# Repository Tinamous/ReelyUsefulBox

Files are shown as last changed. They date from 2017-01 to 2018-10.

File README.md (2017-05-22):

Reely Useful Box - SMD Reel storage and dispenser.
==================================================

SMD reel storage and dispenser based on a Really Useful Storage Box.

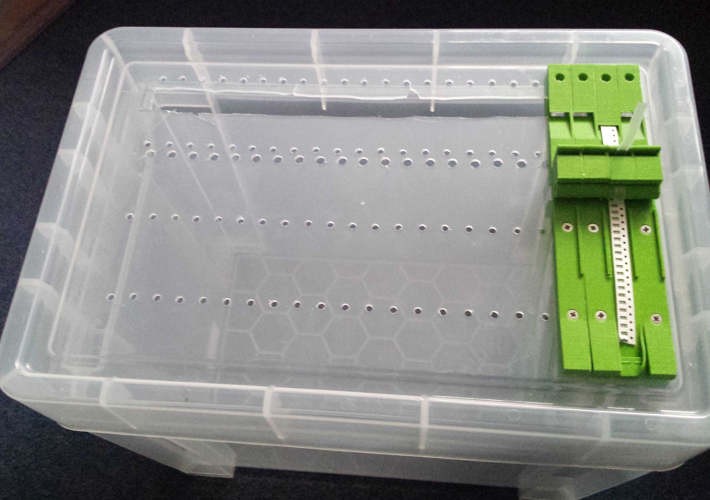
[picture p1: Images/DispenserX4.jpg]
Part built dispenser


Each reel is held and dispensed individually.
The box will hold 25 individual reels (assuming standard 8mm tape for resistors/capacitors).
Each reel holder is 13mm wide. For wider tape/reels this could be doubled to keep to the same hole grid.
Each reel holder is made of 3 different printed parts (1x Top dispenser, 1x reel holder top, 2x reel arms).
Component counter option with LED and photodiode counting of the tape holes.

You can have as few as you want, or as many (well 25 per box and as many boxes as you need).

All design files are Openscad and .stl for direct printing. I found it best to print with a brim as these are long parts and have a tendency to warp at the ends.

##MountingPlate

This is the drilling guide. You can either print it out and drill, or laser cut some acrylic with it.

* Open the .svg file in Inkscape and print this out. 
* It's bigger than A4/Letter, do not scale it! (The box is bigger than A4 length ways so you will need a couple of these for the full 25 way box).
* Stick the sheet to the box lid, allow a margin of about 4mm around the edges where the lid inner curves up (remember the reel holder top has to fit inside).
* Ensure the holes line up with the Dispenser.
* Drill the holes. 
** 4MM for the M3 screw holes (4x).
** 5mm for the LED insert.
** 9-10mm for the square tape hole. This is likely to crack the lid in the process, maybe drill 4 M3.5 holes at each corner and cut, or cut out the entire length of all the sections with a dremel of something  (Be VERY careful if you use a knife, the lid is very tough!).

##Dispenser

This sits on the top of the lid. 

Print in any color you like, you can color code the dispensers to match your components. I'm using:

* 1206 Resistors: Red
* 0805 Resistors: Green
* 1206 Capacitors: White
* 0805 Capacitors: Grey
* 1206 LEDs (Blue): Blue
* Other: Bronze

Original inspiration taken from http://www.thingiverse.com/thing:1080195 with modifications.

* Print this on it's side without supports but with a brim.
* 4 mounting holes for M3 countersunk machine screws.
* A small hole that aligns with the holes in the tape and accepts a 3mm LED underneath.
* The tape film wraps around the block on the top and exits vertically, so pulling the tape film up advances the tape and removes the film.
* Of you can just leave the film on if you want to cut of a section of tape.
* The top block has a hold in the back. Use a M3 heatfit   insert in here if you want to use the component usage sensor block.

## ReelHolder-Top (ReelHolder.scad/ReelHolder.stl)

This sits inside the box to hold the reel arms and is screwed to the lid with the dispenser on the top.

* Print without supports but with a brim as this tends to warp at the edges.
* Fit 3x or 4x M3 HeatFit inserts (Do not fit the one by the square cut out if you wish to use the ComponentUsageSensor block.
* The M5 hole allows a 3mm LED to be pushed through into the dispenser 

## ReelHolder-Arm

These hold the reel and is mounted in the ReelHolder-Top.

* Print 2x of these for each arm.
* These push together either side of the reel and the ReelHolder-Top
* For the end ones you may wish to use a M3 HeatFit insert and small machine screw to hold the tops together if you don't have a tight fit.
* If the arms are not a good fit together change the value of cyinderMatingTollerance in the OpenScad file. I found 0.4 worked well, 0.2 was very tight.
* You may also like to shorten these arms. The variable armHeight sets the length of these. 150mm should allow the reel to be pulled to one side to be replaced.

## Parts Required:

* M3 Heatfit insert Part 1010655 http://www.insertsdirect.com/cgi-bin/sh000001.cgi?WD=1010655&PN=unheaded-heatfit-insert%2ehtml#a1010655
* M3 x 20mm countersunk machine screw (x5 per reel)
* M3 x 6mm countersunk machine screw (x1 for end reels only, or x2 per reel if you need to keep the reel arms together).
* 19XL Really Useful Box http://www.ryman.co.uk/really-useful-storage-box-19xl-litre
* PLA.
* Drills: 4mm, 5mm, 9 or 10mm.
* SMD devices on reels!

## Printer Settings

* Printer: Ultimaker 2 Extended+
* Print Sequence: One at a Time
* Profile: Fast print
** Layer Height: 0.15
** Infil: 20%
** Speed: 60 mm/s
** Wall Thickness: 0.7mm
** Top/Bottom Thickness: 0.75mm
* Build Plate Adhesion: Brim
* Support: None

## Electronics

The dispenser is designed to have a LED/PhotoTransistor pair either side of the tape to count the holes in the tape as they pass. See PCB folder for
instructions on the counter and LED PCB.

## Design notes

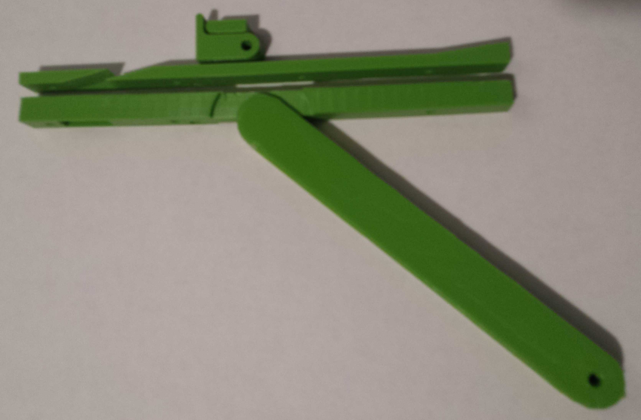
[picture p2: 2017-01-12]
Images/FittingTogether.jpg

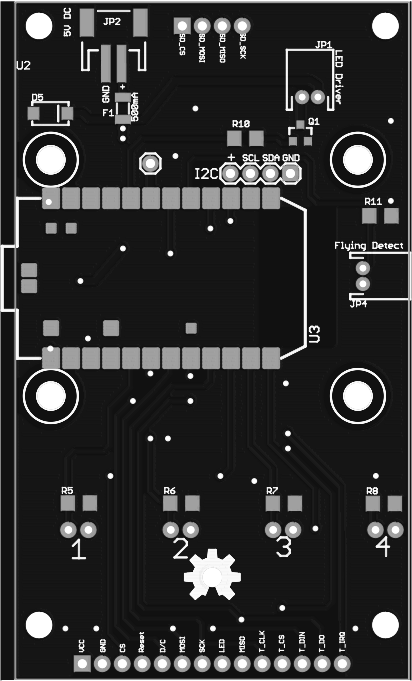
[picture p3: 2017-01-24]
PCB/Images/top.png

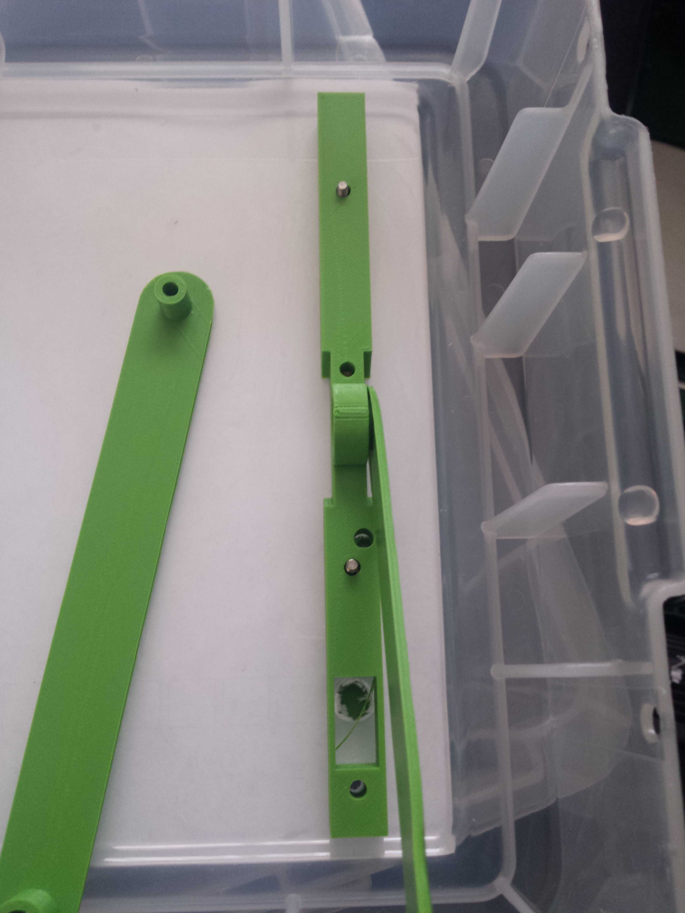
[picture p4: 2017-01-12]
Images/FittingTheArms.jpg

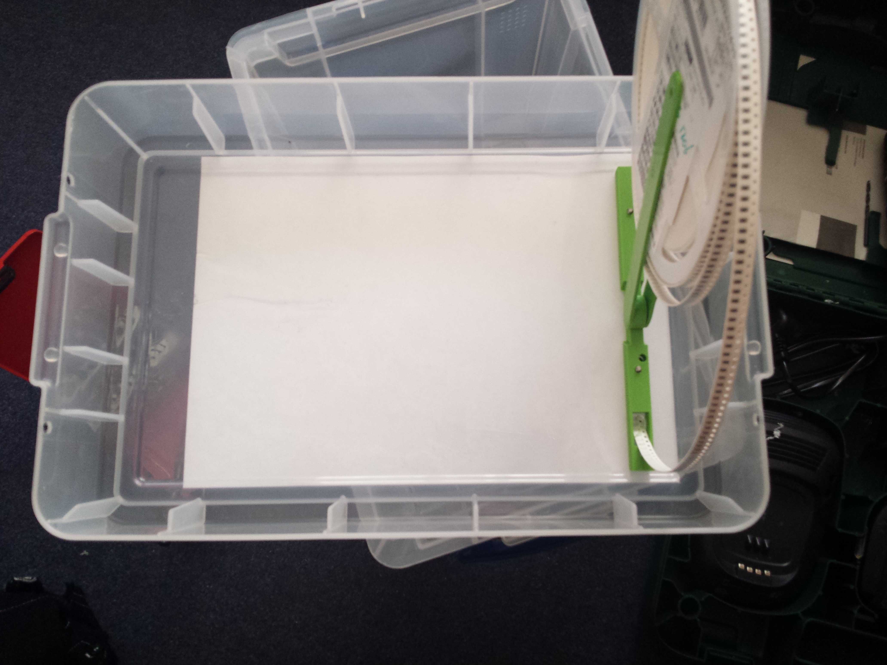
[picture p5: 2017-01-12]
Images/ReelHolderUnderneath.jpg

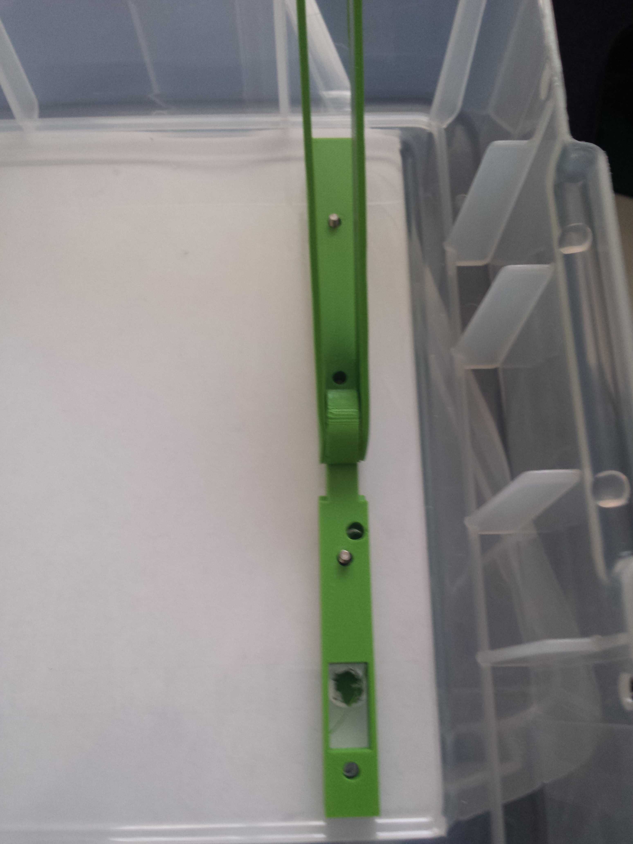
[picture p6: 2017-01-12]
Images/ReelHolderTop.jpg

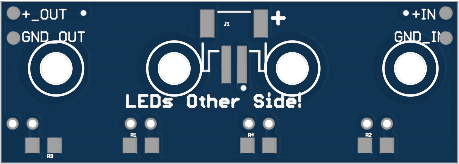
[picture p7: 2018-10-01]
PCB/Images/V2/leds_top.png

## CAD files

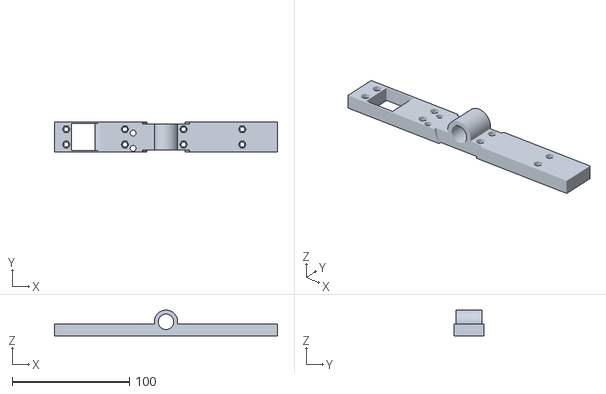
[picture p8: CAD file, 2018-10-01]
13mmVersion/ReelHolder-2Wide.stl
190.0 x 25.9 x 22.0

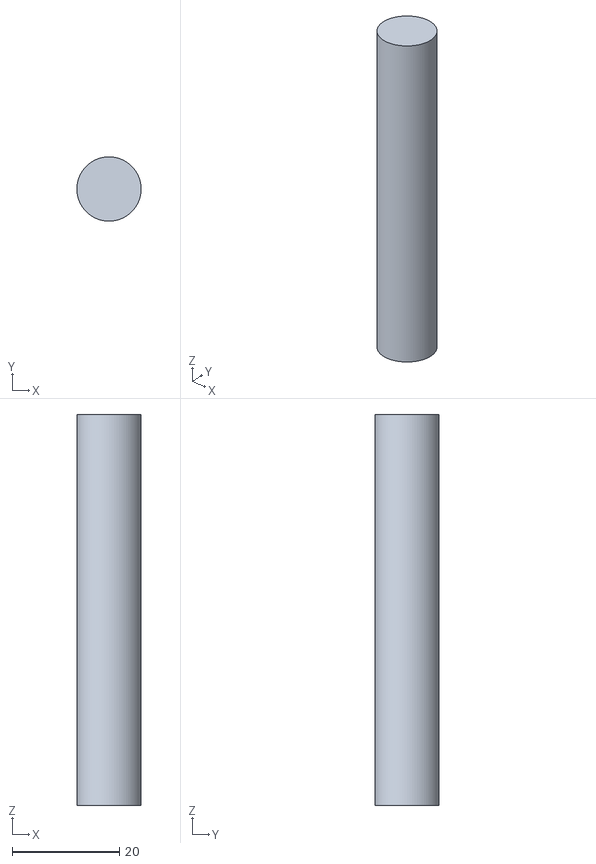
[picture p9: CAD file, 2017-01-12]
Alternative/ReelRod.stl
12.0 x 12.0 x 73.0

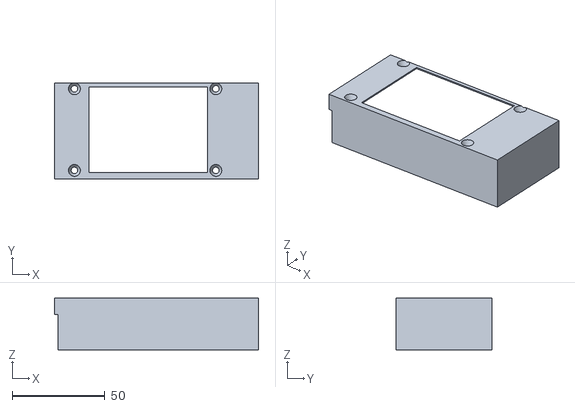
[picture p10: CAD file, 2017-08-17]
Case/DisplayCase.stl
110.0 x 51.5 x 28.0

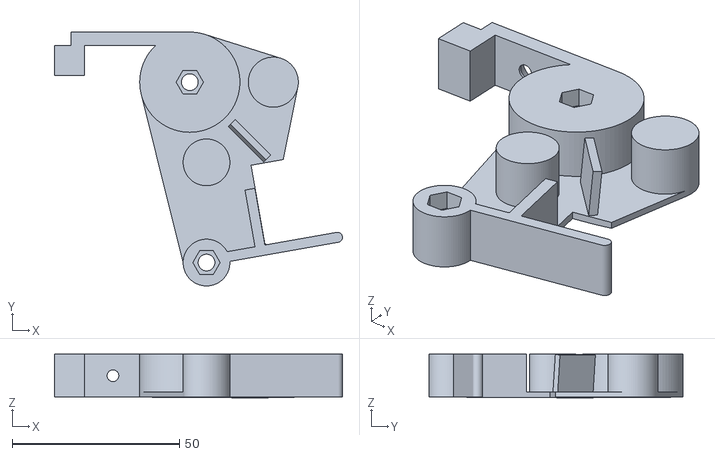
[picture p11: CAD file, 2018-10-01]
ComponentCatcher-13mm.stl
86.2 x 76.0 x 13.0

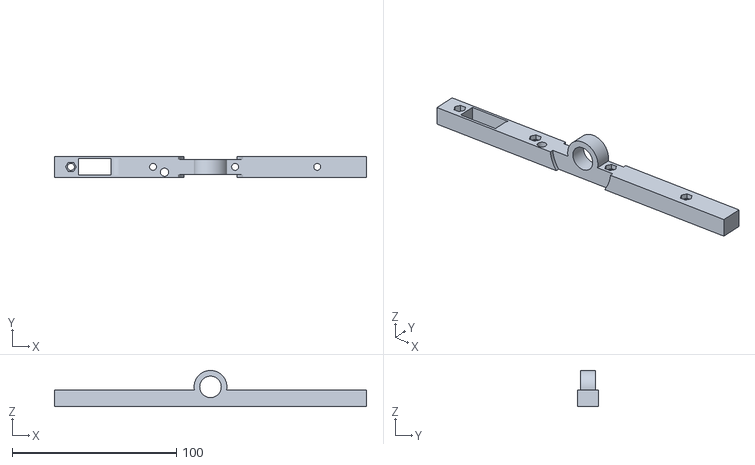
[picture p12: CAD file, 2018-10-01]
13mmVersion/ReelHolder.stl
190.0 x 12.8 x 22.0

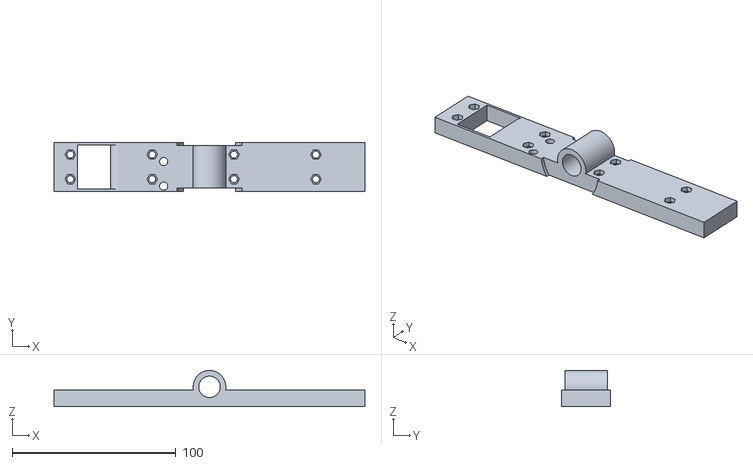
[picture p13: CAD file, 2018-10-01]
ReelHolder-2Wide.stl
190.0 x 29.9 x 22.0

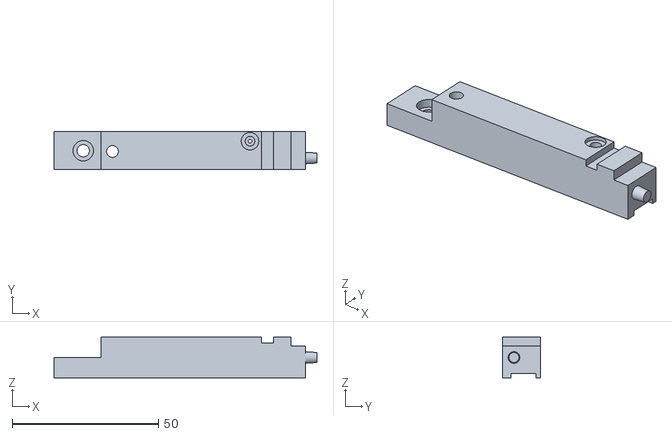
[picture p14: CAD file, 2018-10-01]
13mmVersion/ComponentUsageSensor-Pin.stl
89.9 x 12.8 x 14.0

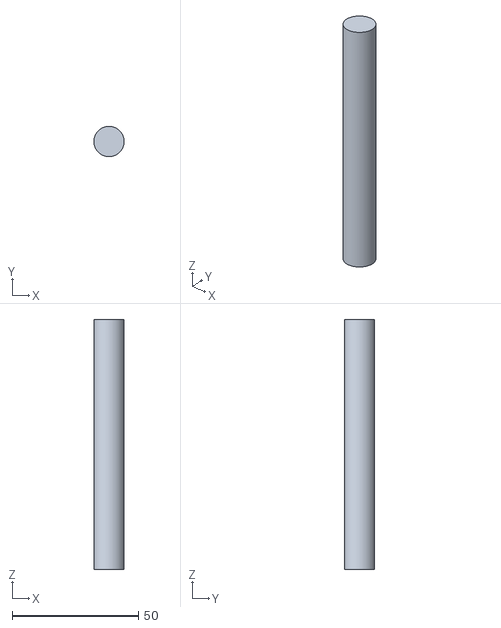
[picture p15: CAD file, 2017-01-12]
Alternative/ReelRod-x7.stl
12.0 x 12.0 x 99.0

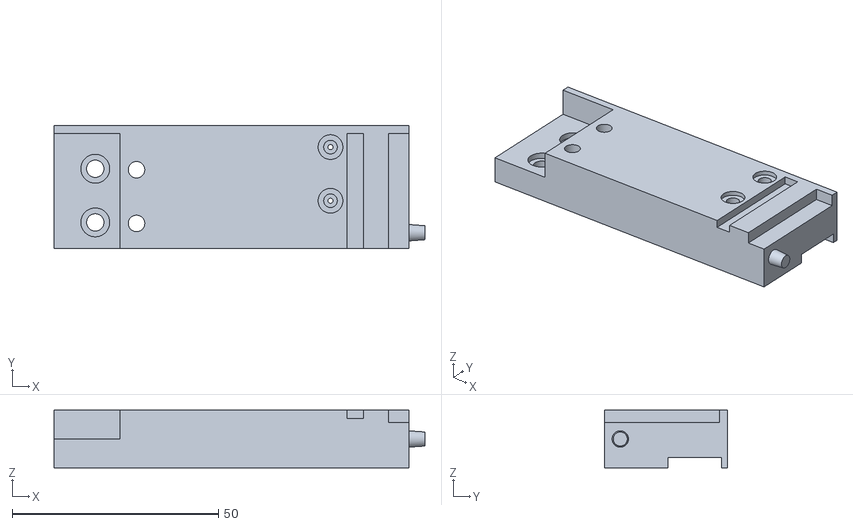
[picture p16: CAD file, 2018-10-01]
ComponentUsageSensor-Pin-LED.stl
89.9 x 29.9 x 14.0

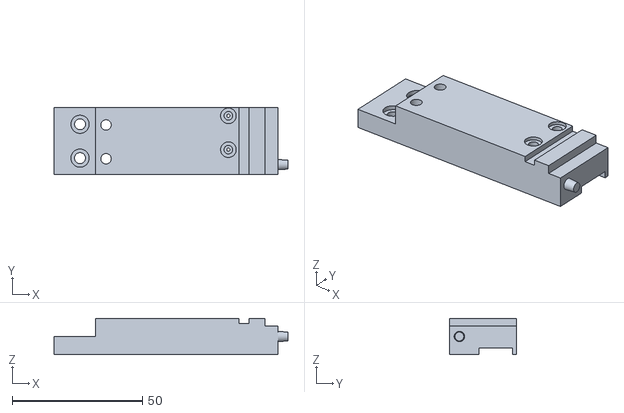
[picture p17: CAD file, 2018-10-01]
13mmVersion/ComponentUsageSensor-Pin-LED.stl
89.9 x 25.9 x 14.0

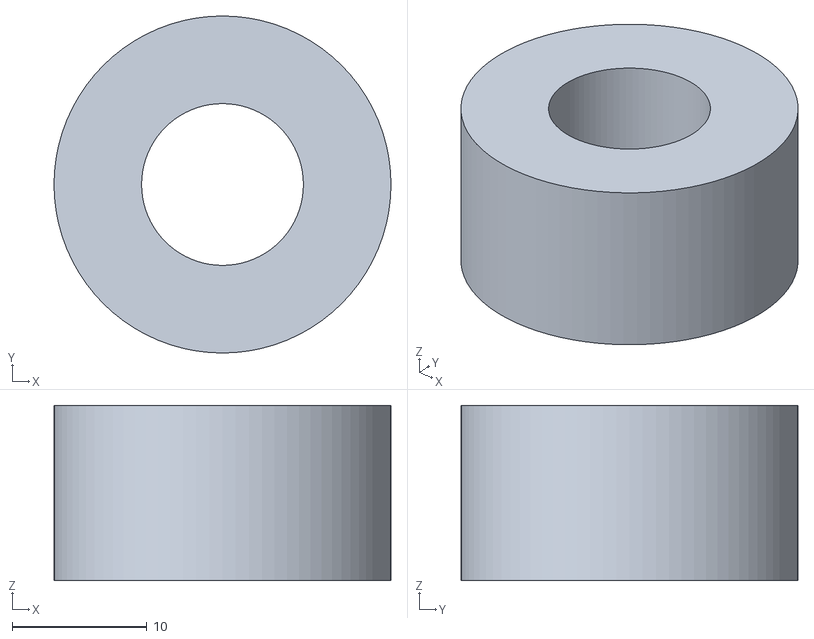
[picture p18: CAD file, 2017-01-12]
Alternative/ReelBlank.stl
25.0 x 25.0 x 13.0

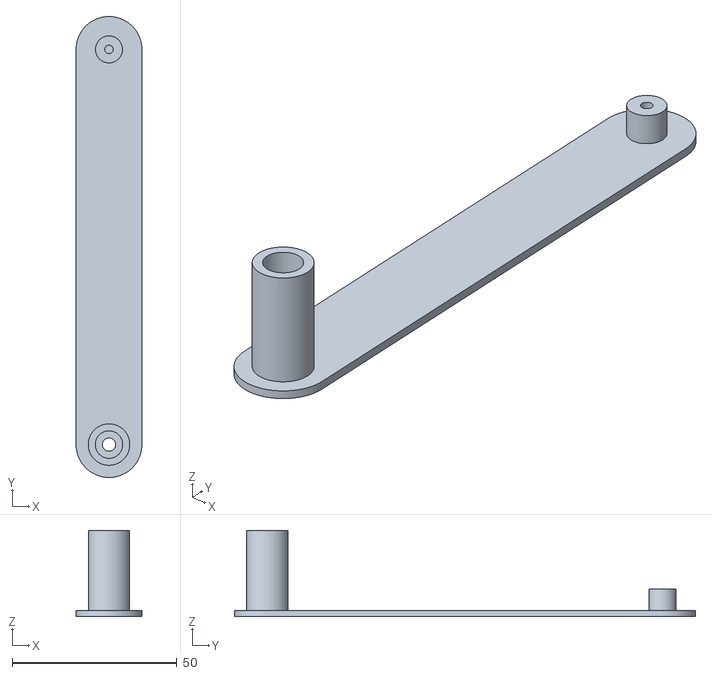
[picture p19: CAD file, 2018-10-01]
ReelHolderArm-2Wide.stl
20.0 x 140.0 x 26.1

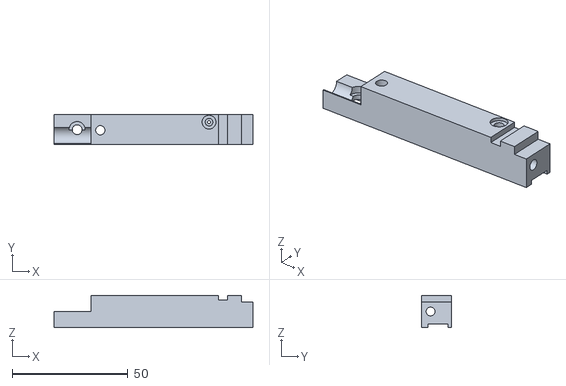
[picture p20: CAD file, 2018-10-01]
13mmVersion/ComponentUsageSensor.stl
86.0 x 12.8 x 14.0

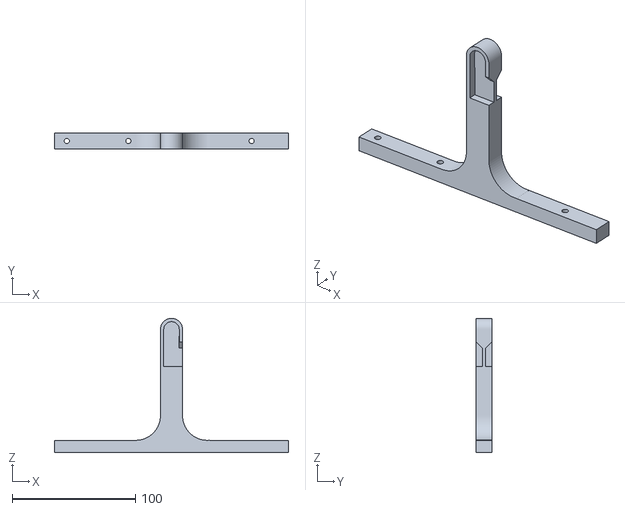
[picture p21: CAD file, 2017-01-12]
Alternative/ReelHolder.stl
190.0 x 13.0 x 109.0

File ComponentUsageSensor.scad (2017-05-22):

$fn = 100;

include <Common.scad>;

// How big or small of a hole to make for the light to come through
// This is printed on its side so allow for printer filament to run in.
tapeHoleSize = 2; // mm - hole side to use for the tape hole light.

// How far before the main block the hole for tape sensing should be.
tapeHoleOffsetFromBlock = 3;

// This should match the roll over block height
// excludes the tape gap.
bodyHeight = 14;
echo("bodyHeight",bodyHeight);

// How long on the x axis this is.
// From Dispenser.
// blockXOffset = 70;
//length = 102; block offset is 87mm
length = blockXOffset - 1; //86; // Or 85?

echo("blockWidth",blockWidth);
actualWidth = blockWidth * numberOfBlocksWide;

// This is 0.5mm less than the main dispenser so that
// the tape doesn't hit as it enters the dispenser.
tapeGap = smdTapeGap +1; // - 0.5;

usePinMount = true;


// Tape Width MUST be set appropriatly
// for numberOfBlocksWide>1 it is assumed this is for
// wide tape and not just to make n blocks in one go.
// Hence tapeWidth must be set for the tap to ensure
// the tape is guided properly.
module cutoutTapePath() {
    // Fattest part is on the right y=0)
    translate([-0.1,blockWidth - (backerWidth + tapeWidth),-0.1]) {
        //#cube([length+1.2, tapeWidth, tapeGap+0.2]);
    }
    
echo ("blockWidth=",blockWidth);
echo ("backerWidth=",backerWidth);
echo ("tapeWidth=",tapeWidth);
echo ("Left offset=",blockWidth - (backerWidth + tapeWidth));
    
    // Put a very slight angle on the block so that the tape comes out
    // at a lower height than would be expected for the smdTapeGap
    // in the dispenser block - so it shouldn't get stuck when feeding through.
    translate([-0.1,actualWidth - (backerWidth + tapeWidth),0]) {
        rotate([0,1,0]) {
            cube([length+0.1, tapeWidth, tapeGap]);
        }
        //translate([0,blockWidth - backerWidth ,0]) {
    }
}

module cutoutMultiTapePath() {
    // Put a very slight angle on the block so that the tape comes out
    // at a lower height than would be expected for the smdTapeGap
    // in the dispenser block - so it shouldn't get stuck when feeding through.
    
    for (rep = [1 : numberOfBlocksWide]) {
        width = blockWidth * rep;
        translate([-0.1,width - (backerWidth + tapeWidth),0]) {
            rotate([0,1,0]) {
                cube([length+0.1, tapeWidth, tapeGap]);
            }
            //translate([0,blockWidth - backerWidth ,0]) {
        }
    }
}
   
// Make a sticky out pointy thing for mounting to the 
// dispenser block.
module mountingPoint() {
    
        // No repetition for multiblocks.
        // Fixed at 7mm up
        translate([length - 0.1, 4, 7]) {
            rotate([0,90,0]) {
                // Component counter mount hole
                // Hole is 4.2mm
                cylinder(d1=4, d2=3.4,  h=4);
            }
    }
}

// Use either this or the mounting point
module horizontalMountingHole() {
// Horizontal hole.
// 20mm screw. 5mm into nut leaves 15mm in the body.
// Don't make shorter as this 
screwHeadDepth = length - 15;
    
    translate([-0.1, 4, 10/2 + smdTapeGap]) {
        rotate([0,90,0]) {
            // Component counter mount hole
            cylinder(d=3.8, h=length+0.2);
            // Screw head sink in.
            cylinder(d=7, h=screwHeadDepth);
        }
    }
}

// Holes for the module to be mounted onto the dispenser.    
module mountingHole() {

    // Needs to be addeed.
    //mountingPoint();
    
    // If used, needs to be subtracted.
    if (!usePinMount) {
        horizontalMountingHole();
    }
    
    // All vertical holes are on a 13mm pitch
    // so 6.5 from edge.
    // Dispenser first hole is 10mm in.
    translate([10, 6.5, 0]) {
       cylinder(d=4.2, h=bodyHeight);
    }

    // Add a cutout for the screw head.
    // Sink it right in otherwise we need a long screw.
    // as it has to go through the 5mm of the dispenser
    // and the 10mm of the rool holder top.
    translate([10, 6.5, tapeGap + 1.5]) {
        //   
       cylinder(d=7, h= bodyHeight);
    }
}

module lightSensorHole() {
    translate([0,0,0]) {
        translate([70 - tapeHoleOffsetFromBlock, blockWidth - backerWidth - tapeHoleOffset,-0.1]) {
            // Small hole all the way up
            // Tape hole is about 1.75 with 4mm spacing
            cylinder(d=1.25, h=bodyHeight - tapeGap + 0.2);
            
            // Bigger hole at top for the sensor to be pushed into
            // Add 0.3mm on to allow for Form2 tight fit.
            // 3mm worked well for UM PLA.
            translate([0,0, tapeGap + 2]) {
                cylinder(d=3 + 0.3, h=bodyHeight - tapeGap);
            }
            
            // And an even bigger hole for the wide part of the sensor.
            // so that the PCB can sit flush onto the block.
            // LED body length is about 5-6 mm.
            // Allow 1mm only for the top part.
            translate([0,0,bodyHeight - 1]) {
                cylinder(d=6, h= 2);
            }
        }
    }
}

// Holes (well hole) for the PCB to use when mounted on-top
// NB: Block needs to be fixed to the dispenser system 
// before the PCB is attached, and the PCB may be 
// shared between different dispensers.
module pcbMountingHoles() {
    
// Just one mounting hole as the LED/diode is already a mounting point.

// How deep in the screw recess should stop 
screwHoleDepth = 6.5;
    
// PCB has LED at 3mm offset
// however it's actually 3.25 (1.5mm backerWidth wall))
// or 3.75 if we use a 2mm backerWidth wall
// So move the mounting hole so that the distance between the LED hole
// and the mouting hole are the same.
pcbLedOffsetFudge = 0.25;
        
    translate([20,6.5 - pcbLedOffsetFudge,0]) {
        //#cylinder(d=8, h= bodyHeight - screwHoleDepth);
        // 6.5 is a little tight for the nut.
        //cylinder(d=6.6, h= bodyHeight - screwHoleDepth, $fn=6);
        
        // Screw head should sit just inside the block above
        // the tape path
        //#cylinder(d=6.6, h= screwHoleDepth);
        // Hole all the way though for the thread.
        #cylinder(d=4, h= bodyHeight + 1.1);
        
        // recess the nut 3.5mm into the part.
        translate([0,0,bodyHeight-7]) {
            #cylinder(d=6.6, h= 2.8, $fn=6);
            
            translate([-5,-5.7/2,0]) {
                #cube([5,5.7,2.8]);
            }
        }
    }
    
    /*
    translate([50,6.5 - pcbLedOffsetFudge,0]) {
        //#cylinder(d=8, h= bodyHeight - screwHoleDepth);
        cylinder(d=6.6, h= bodyHeight - screwHoleDepth, $fn=6);
        cylinder(d=4.5, h=bodyHeight + 0.1);
    }
    */
}

// Remove space for the display pins to protrude through
// blocks.
module pcbPinsCutouts() {
        
    // 3mm in. (This is the top one).
    // It also needs to allow for the LED drive
    // connector which is 12mm down the PCB
    translate([0, 0, bodyHeight-7]) {
        cube([16,blockWidth,7.1]);
    }
    
    // 84mm in. End nearest the dispenser block
    // allow for main display pins.
    translate([81, 0, bodyHeight-3]) {
        cube([6,blockWidth,3.1]);
    }
    
    // Remove space for the OSH LED. 
    // This is only needed on the middle 2 
    // blocks but we don't knowh which two they are.
    oshLedXPosition=73; //mm
    translate([oshLedXPosition-2, 0, bodyHeight-2]) {
        cube([4,blockWidth,2.1]);
    }
}

difference() {
    union() {
        // Main block body.
        cube([length, actualWidth, bodyHeight]);
        
        if (usePinMount) {
            
            if (repeatTape) {
                // repeat pins might cause problems for tollerance.
                for (rep = [0 : numberOfBlocksWide -1]) {    
                    repYOffset = rep * 13;
                    translate([0,repYOffset,0]) {
                        mountingPoint();
                    }
                }
            } else {
                mountingPoint();
            }
        }
    }
    union() {
        if (repeatTape) {
            cutoutMultiTapePath();
        } else {
            cutoutTapePath();
        }
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

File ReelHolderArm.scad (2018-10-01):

$fn=100;


include <Common.scad>;

supportWidth = (blockWidth * numberOfBlocksWide) - 0.25; // To match block width used in the dispenser.

// X Axis length
armLength = 20;
armSupportLength = 2;
armHeight = 120;
armWidth = 1.8; // 0.6mm nozzle

reelTubeDiameter = 12.6;

smallerMatingDiameter = 8;

// How mech space to leave between the inner and outer cylinder.
// 0.2 on UM2+ left a very tight fit.
// 0.3 on UM2+ with RigidInk PLA also a tight fit.
// 0.5 should be easy fit, then use M3 countersunk 12mm screws to join.
cylinderMatingTollerance = 0.5;

// How much to redice the height of the end cylinders to ensure one fits fully in the other
//cylinderHeightTollerence = 2;

module arm() {
    /*
    // Test cube to check assumption on height.
    translate([20,0,0]) {
        cube([10,10,15]);
    }
    */
    
    difference() {
        union() {
            // Fat outer cylinger.
            translate([armLength/2, 0, 0]) {
                translate([0, 0, 0]) {
                    // Create the large outside curved edge.
                    // cut hole in for contersinking M3 screw
                        cylinder(d=armLength, h=armWidth);
                }
                
                // Create a large pin then subtract a small pin
                // + tollerance to allow two ends to mate
                // to hold in place.
                
                translate([0,0,0])  {
                    difference() {
                        union() {
                          cylinder(d=reelTubeDiameter, h=supportWidth - armWidth );
                        }
                    
                        union() {
                            translate([0,0,armWidth]) {
                                cylinder(d=smallerMatingDiameter + cylinderMatingTollerance, h=supportWidth - armWidth);
                            }
                        }
                    }
                }
            }

            
            // Main body
            translate([0,0, supportWidth-armWidth,0]) {
                cube([armLength, armHeight, armWidth]) ;
            }
            
            // Small cylinder end
            translate([armLength/2, armHeight,0]) {
                    translate([0, 0, 0]) {
                       cylinder(d=armLength, h=armWidth);
                    }
                    
                    // Smaller inner mating pin
                    // with hole for M3 brass inser
                    // Keep this short to reduce the maiting surface
                    // area when connected to the fatter cylidner
                    // otherwise it's difficult to seperate
                    smallCylinderHeight = (blockWidth-3);
                    translate([0,0,0]) { 
                        difference() {
                            union() {
                                translate([0,0,0]) { 
                                    // 1mm fudge tollerance.
                                    cylinder(d=smallerMatingDiameter + 0.2, h=smallCylinderHeight - armWidth - 1);
                                }
                            }
                            union() {
                                // Hole to screw into with an M3 machine screw
                                translate([0,0,armWidth]) { 
                                    cylinder(d=3.0, h=smallCylinderHeight + armWidth);
                                }
                                // small countersink to help get the screw started
                                translate([0,0, smallCylinderHeight - armWidth - 1 - 2]) { 
                                    cylinder(d1=3.0,d2=4.2, h=2.01);
                                }
                            }
                        }
                        
                    }
            }
        }
        union() {
            translate([armLength/2, 0, -0.5]) {
                    // Countersink hole at top
                    cylinder(d1=7, d2=3.4, h=armWidth+1);
                    // Ensure the hole runs all the way through
                    cylinder(d=3.4, h=supportWidth+1);
            }
        }
    }
}


//rotate([-90,0,0]) {
    arm();
//}

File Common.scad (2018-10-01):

// Height between base and wrapper.
// for fat components (e.g. LEDs) increase this.
// NB: Tape enterance is not adjusted for this.
smdTapeGap = 2;
// smdTapeGap = 3; // for LEDs

// 1.75mm offset because that's the offset on the tape.
// Was 1.5
tapeHoleOffset = 1.75; // mm

// How thick the back (well side) support structure is
// the tape sits against this.
backerWidth = 1.5; // 1.5;
// 8mm tape + backer = 9.5mm, 
// 13mm block -> 3.5mm play on the left.
// 12mm tape + backer = 13.5 >> block width

// How wide the thing is.
blockWidth = 15;

// How many block units (e.g. 13mm's) wide
// Mounting holes will be duplicated but 
// LED hole not.
// Be sure to set tapeWidth correctly for the wide tape.
numberOfBlocksWide = 1;

// How much to remove off the block width to allow
// for printer tollerance so that each block
// fits in the 13mm grid.
// Set to 6.5 to test screw centers.
// Set to 9.75 to test (3mm offset) for LED for component counter and dispenser.
// Set to 1.5 + 1.75 (3.25) to test (3mm offset) for LED for arm
// Set to 4 to test horizontal coupler.
// Set to 0.25 for normal printing.
blockPrinterTollerance = 0.15; //0.25;

// Tape Width MUST be set appropriatly
// for numberOfBlocksWide>1 it is assumed this is for
// wide tape and not just to make n blocks in one go.
// Hence tapeWidth must be set for the tap to ensure
// the tape is guided properly.

// How much space to allow for the tape.
// Actually 8mm but add 0.5 to allow it to move easily
// LED tape is 12.5mm wide so use 13mm
tapeWidth = 8.5;

// If the tape is to be repeated for each block wide
// typically if making n component sensor blocks in one go 
// e.g. 4 unit block.
// if just wide tape, set to false and set tape width.
repeatTape = true;

// How far along the dispenser the top block
// for film removal is.
// 11mm in the original
// 70mm for the 
//blockXOffset = 70;
// PCB is 86mm long.
blockXOffset = 87;

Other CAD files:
ReelHolderArm.stl
13mmVersion/ComponentCatcher-2Wide.stl
ReelHolder.stl
ComponentCatcher.scad
13mmVersion/ComponentCatcher.stl
13mmVersion/ComponentUsageSensor-Pin-4Wide-MultiTape.stl
13mmVersion/Dispenser-2Wide.stl
13mmVersion/Dispenser.stl
13mmVersion/ReelHolderArm-2Wide.stl
13mmVersion/ReelHolderArm.stl
Alternative/ReelBlank.scad
Alternative/ReelHolder.scad
Alternative/ReelRod.scad
Case/DisplayCase.scad
ComponentCatcher.stl
ComponentUsageSensor-Pin-4Wide-MultiTape.stl
ComponentUsageSensor-Pin.stl
ComponentUsageSensor.stl
Dispenser-2Wide.stl
Dispenser.scad
Dispenser.stl
MountingPlate.scad
MountingPlateV2mm.dxf
MountingPlatev2-smaller-inkscaped.dxf
ReelHolder.scad
ReelHolder2.scad

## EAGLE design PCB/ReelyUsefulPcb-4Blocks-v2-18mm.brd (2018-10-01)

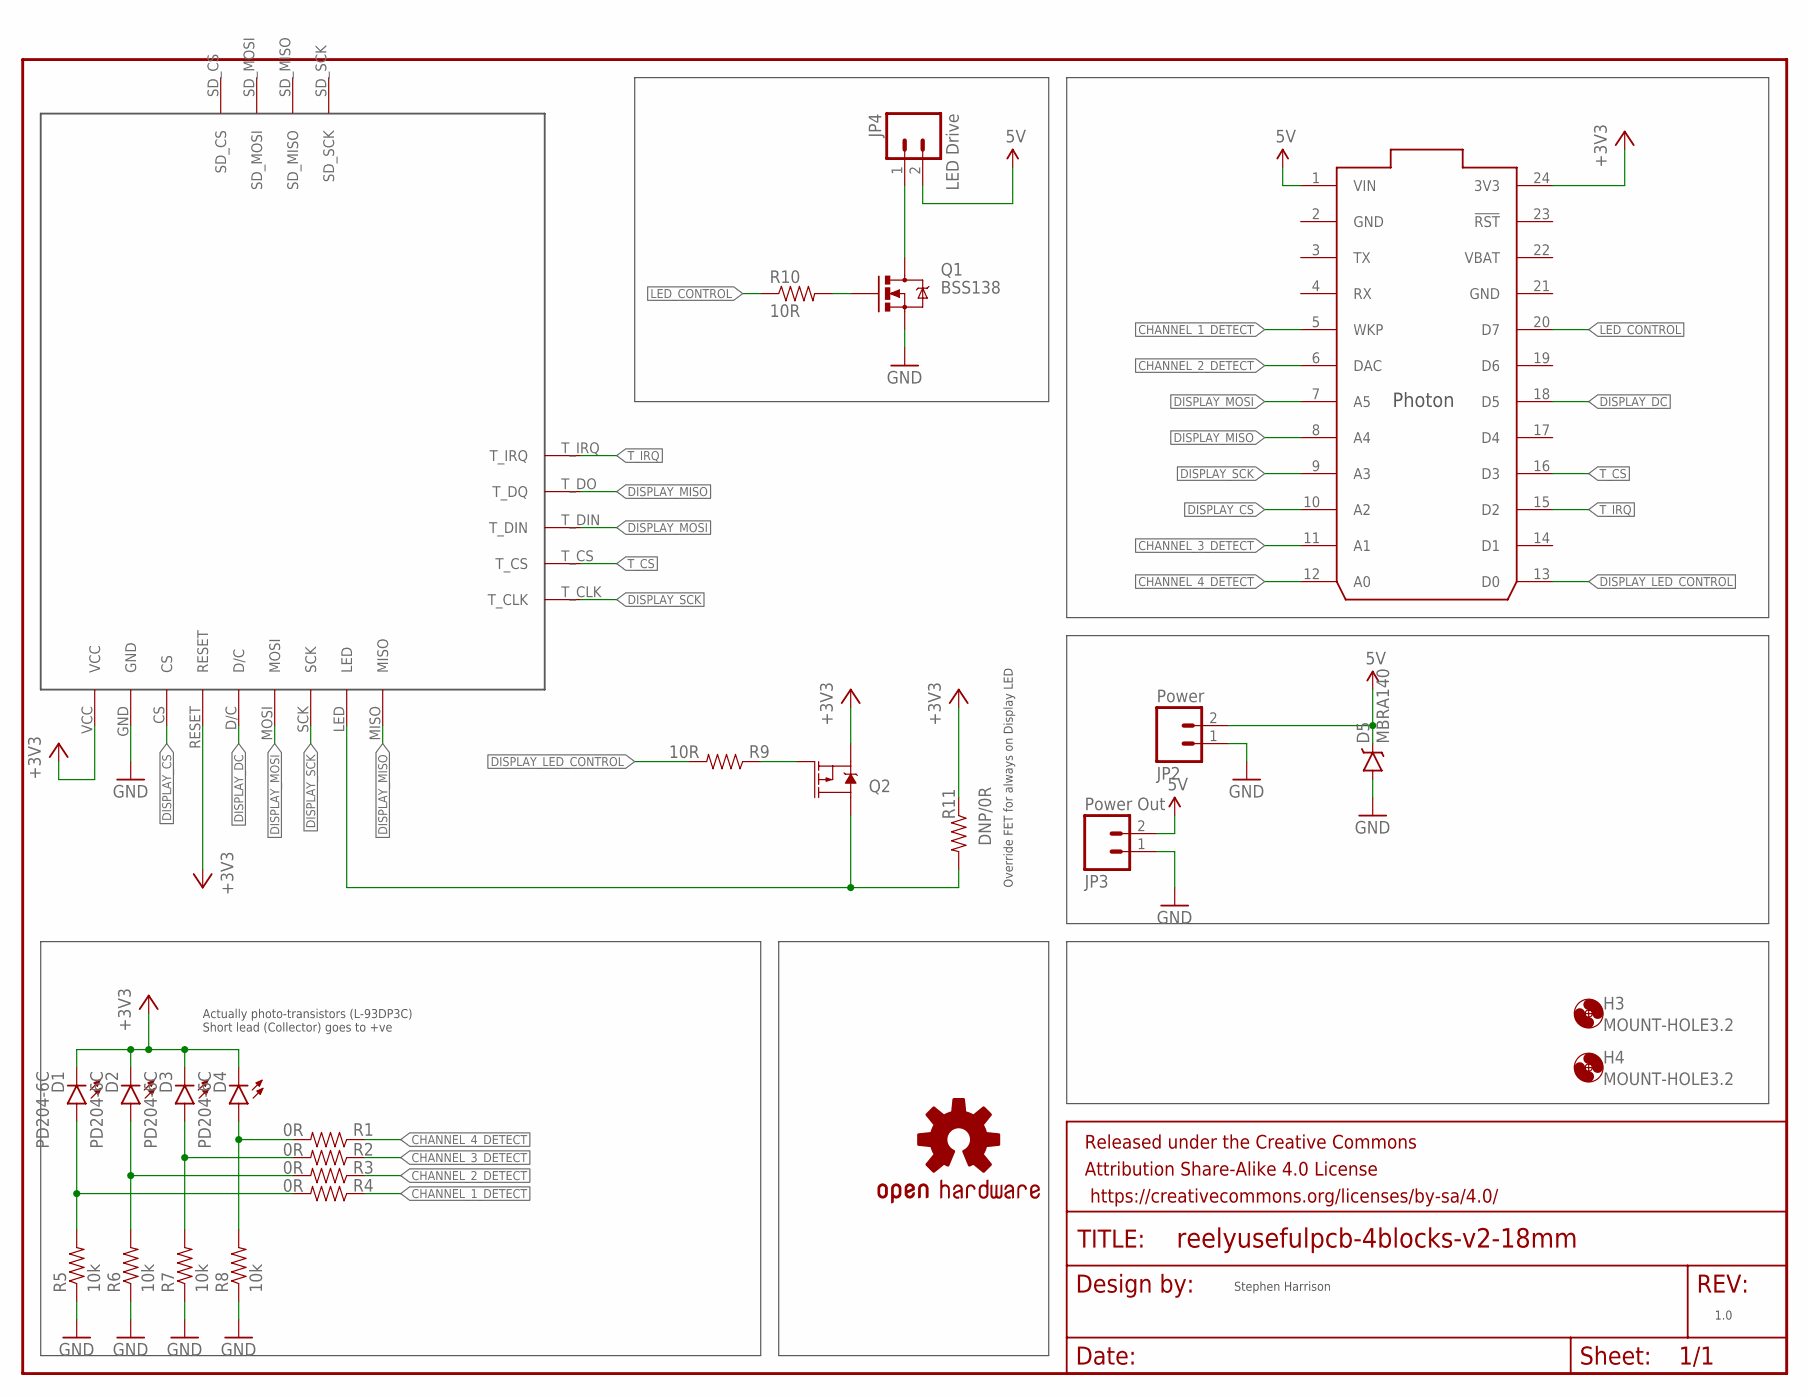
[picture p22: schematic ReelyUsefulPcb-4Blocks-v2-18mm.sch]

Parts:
D1, D2, D3, D4: PD204-6C; LED3MM
D5: MBRA140; SMA-DIODE
FRAME1: FRAME-LETTER; CREATIVE_COMMONS
H3, H4: MOUNT-HOLE3.2; 3,2
JP2: Power; JST-2-SMD
JP3: Power Out; JST-2-SMD
JP4: LED Drive; JST-2-SMD
LOGO1: OSHW-LOGOL; OSHW-LOGO-L
Q1: BSS138; SOT23-3@1; FARNELL 9845330
Q2: 2.5A/30V/105mΩ; SOT23-3
R1, R2, R3, R4: 0R; 1206
R5, R6, R7, R8: 10k; 1206
R9, R10: 10R; 1206
R11: DNP/0R; 1206
U2: TJCTM240NO-MOUNTING-HOMES; TJCTM240-NOHOLES
U3: PHOTON_SMD

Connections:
5V: D5.C, JP2.2 (1), JP3.2 (1), JP4.2 (1), U3.1 (VIN)
+3V3: D1.K (C), D2.K (C), D3.K (C), D4.K (C), Q2.2 (S), R11.1, U2.RESET, U2.VCC, U3.24 (3V3)
CHANNEL_1: D1.A, R4.2, R5.2
CHANNEL_1_DETECT: R4.1, U3.5 (WKP)
CHANNEL_2: D2.A, R3.2, R6.2
CHANNEL_2_DETECT: R3.1, U3.6 (DAC)
CHANNEL_3: D3.A, R2.2, R7.2
CHANNEL_3_DETECT: R2.1, U3.11 (A1)
CHANNEL_4: D4.A, R1.2, R8.2
CHANNEL_4_DETECT: R1.1, U3.12 (A0)
DISPLAY_CS: U2.CS, U3.10 (A2)
DISPLAY_DC: U2.D/C, U3.18 (D5)
DISPLAY_LED_CONTROL: R9.2, U3.13 (D0)
DISPLAY_MISO: U2.MISO, U2.T_DO (T_DQ), U3.8 (A4)
DISPLAY_MOSI: U2.MOSI, U2.T_DIN, U3.7 (A5)
DISPLAY_SCK: U2.SCK, U2.T_CLK, U3.9 (A3)
GND: D5.A, JP2.1 (2), JP3.1 (2), Q1.2 (S), R5.1, R6.1, R7.1, R8.1, U2.GND, U3.2 (GND), U3.21 (GND)
LED_CONTROL: R10.1, U3.20 (D7)
unnamed: JP4.1 (2), Q1.3 (D)
unnamed: Q2.1 (G), R9.1
unnamed: Q1.1 (G), R10.2
unnamed: Q2.3 (D), R11.2, U2.LED
T_CS: U2.T_CS, U3.16 (D3)
T_IRQ: U2.T_IRQ, U3.15 (D2)
VBAT: U3.22 (VBAT)

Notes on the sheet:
Actually photo-transistors (L-93DP3C) Short lead (Collector) goes to +ve
1.0
Stephen Harrison
Override FET for always on Display LED

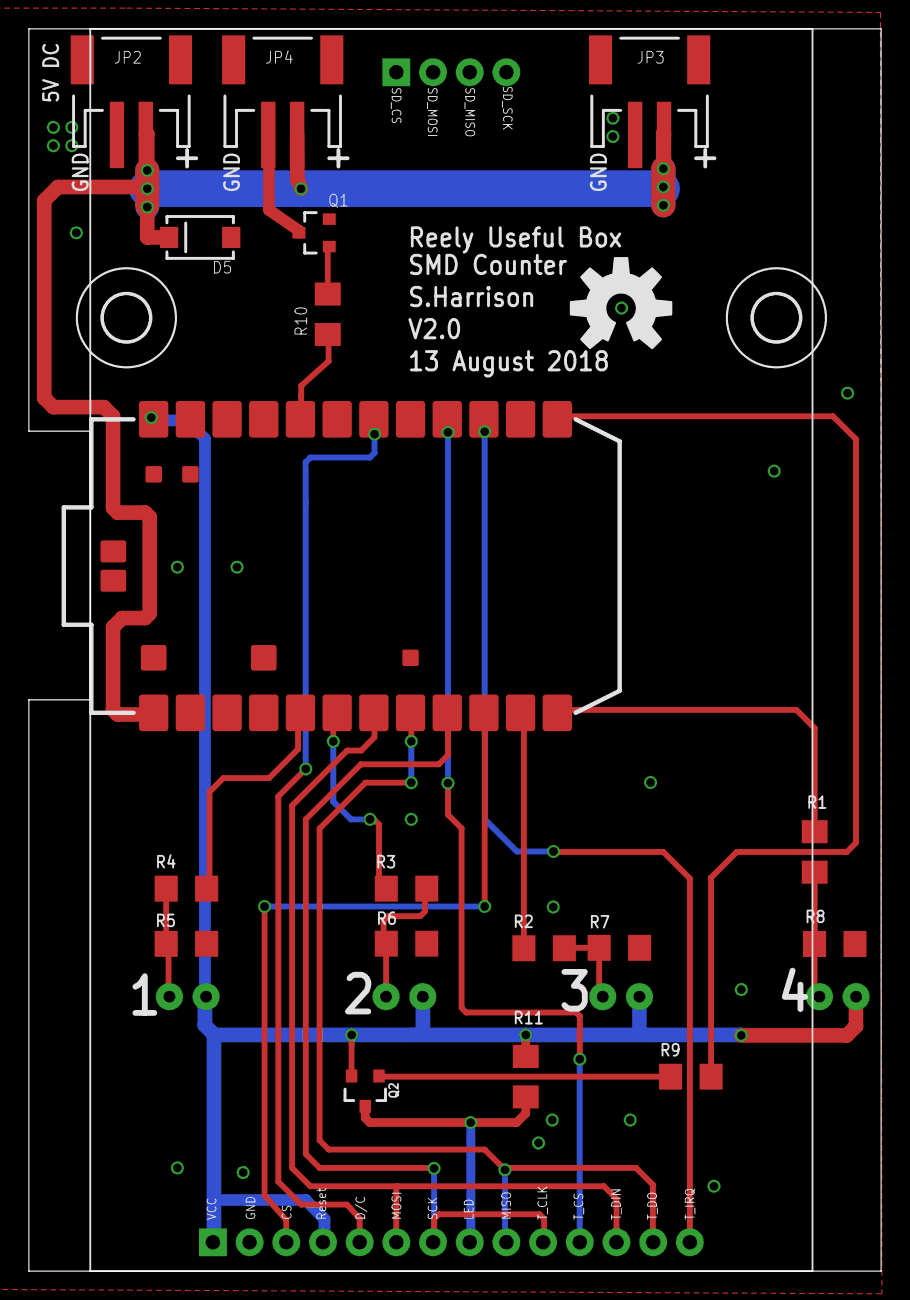
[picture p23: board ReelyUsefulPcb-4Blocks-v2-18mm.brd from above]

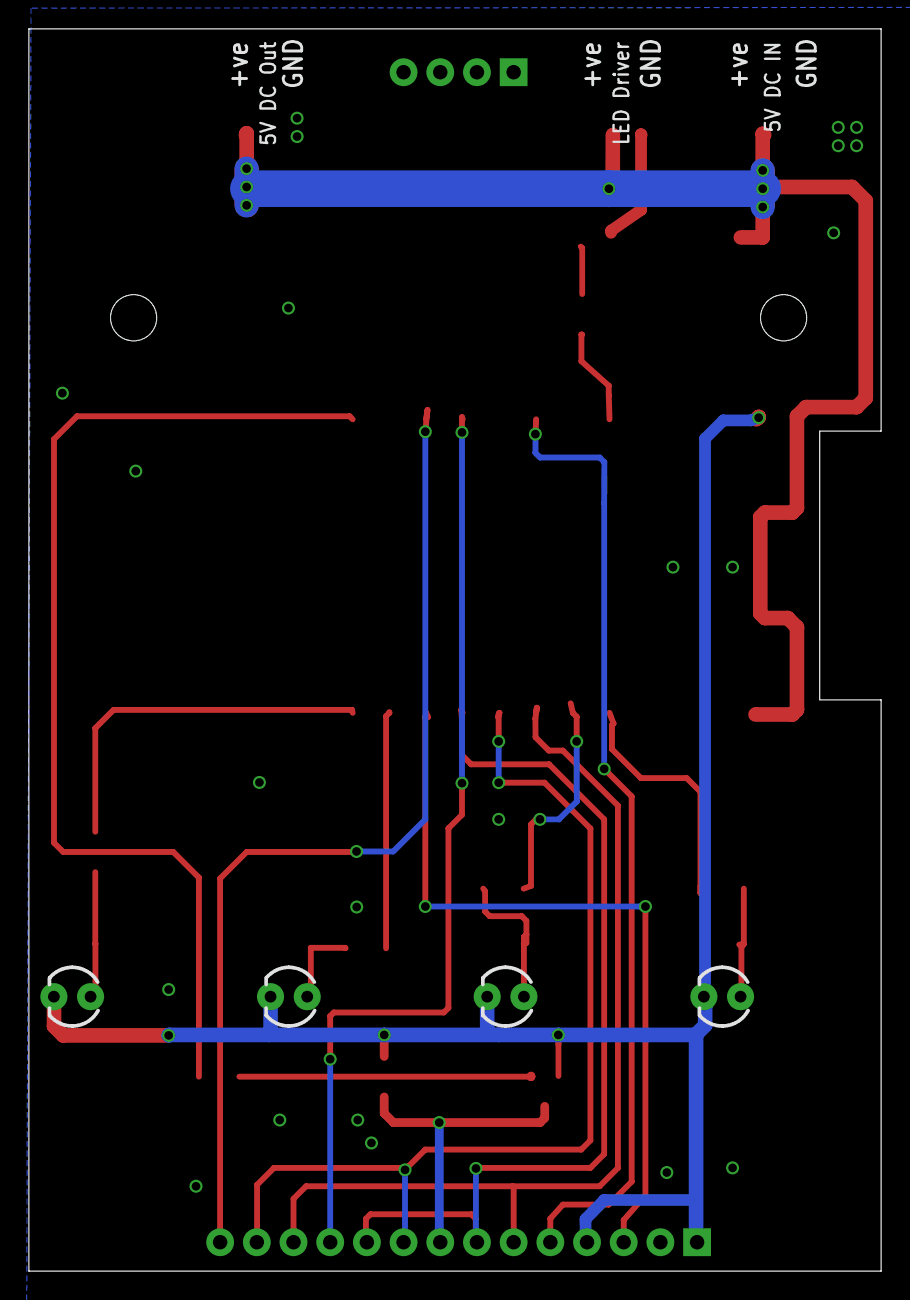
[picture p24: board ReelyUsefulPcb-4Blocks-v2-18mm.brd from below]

Board: 2 copper layers, 59.0 x 86.0 mm, 27 parts (4 on the bottom side), 24 nets.

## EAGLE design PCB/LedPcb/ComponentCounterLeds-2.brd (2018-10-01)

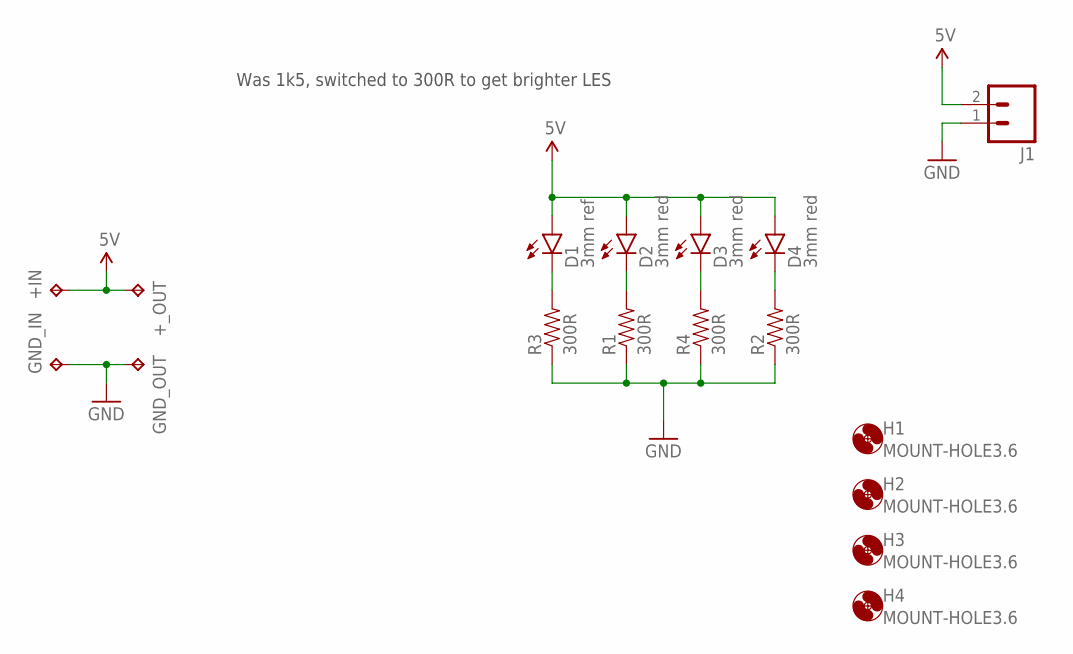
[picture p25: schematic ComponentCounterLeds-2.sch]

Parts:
+IN: TPTP15R; TP15R
+_OUT: TPTP15R; TP15R
D1: 3mm ref; LED3MM-NS
D2, D3, D4: 3mm red; LED3MM-NS
GND_IN: TPTP15R; TP15R
GND_OUT: TPTP15R; TP15R
H1, H2, H3, H4: MOUNT-HOLE3.6; 3,6
J1: M02-JST-2MM-SMT; JST-2-SMD; FARNELL 9492615
R1, R2, R3, R4: 300R; 1206

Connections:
5V: +IN.TP, +_OUT.TP, D1.A, D2.A, D3.A, D4.A, J1.2 (1)
GND: GND_IN.TP, GND_OUT.TP, J1.1 (2), R1.1, R2.1, R3.1, R4.1
unnamed: D2.K (C), R1.2
unnamed: D4.K (C), R2.2
unnamed: D3.K (C), R4.2
unnamed: D1.K (C), R3.2

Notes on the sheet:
Was 1k5, switched to 300R to get brighter LES

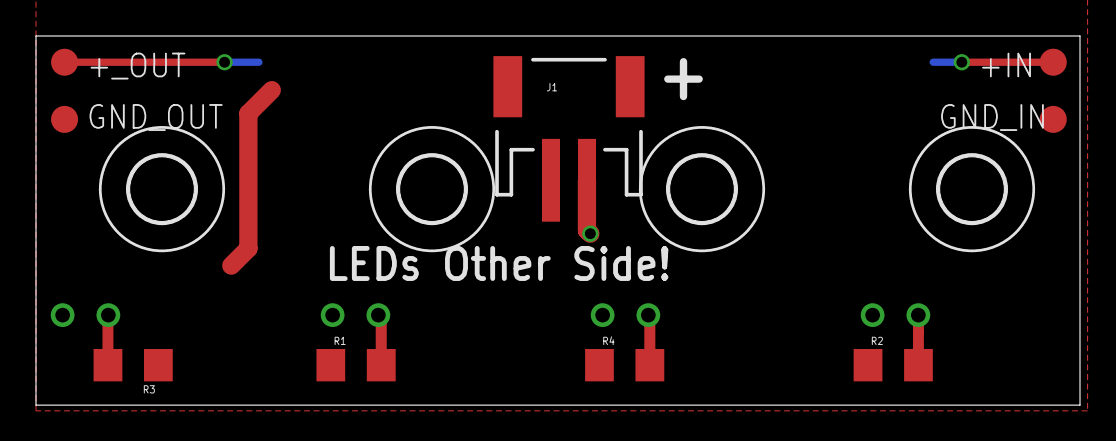
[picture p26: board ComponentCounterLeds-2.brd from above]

Board: 2 copper layers, 58.0 x 20.5 mm, 17 parts (0 on the bottom side), 6 nets.

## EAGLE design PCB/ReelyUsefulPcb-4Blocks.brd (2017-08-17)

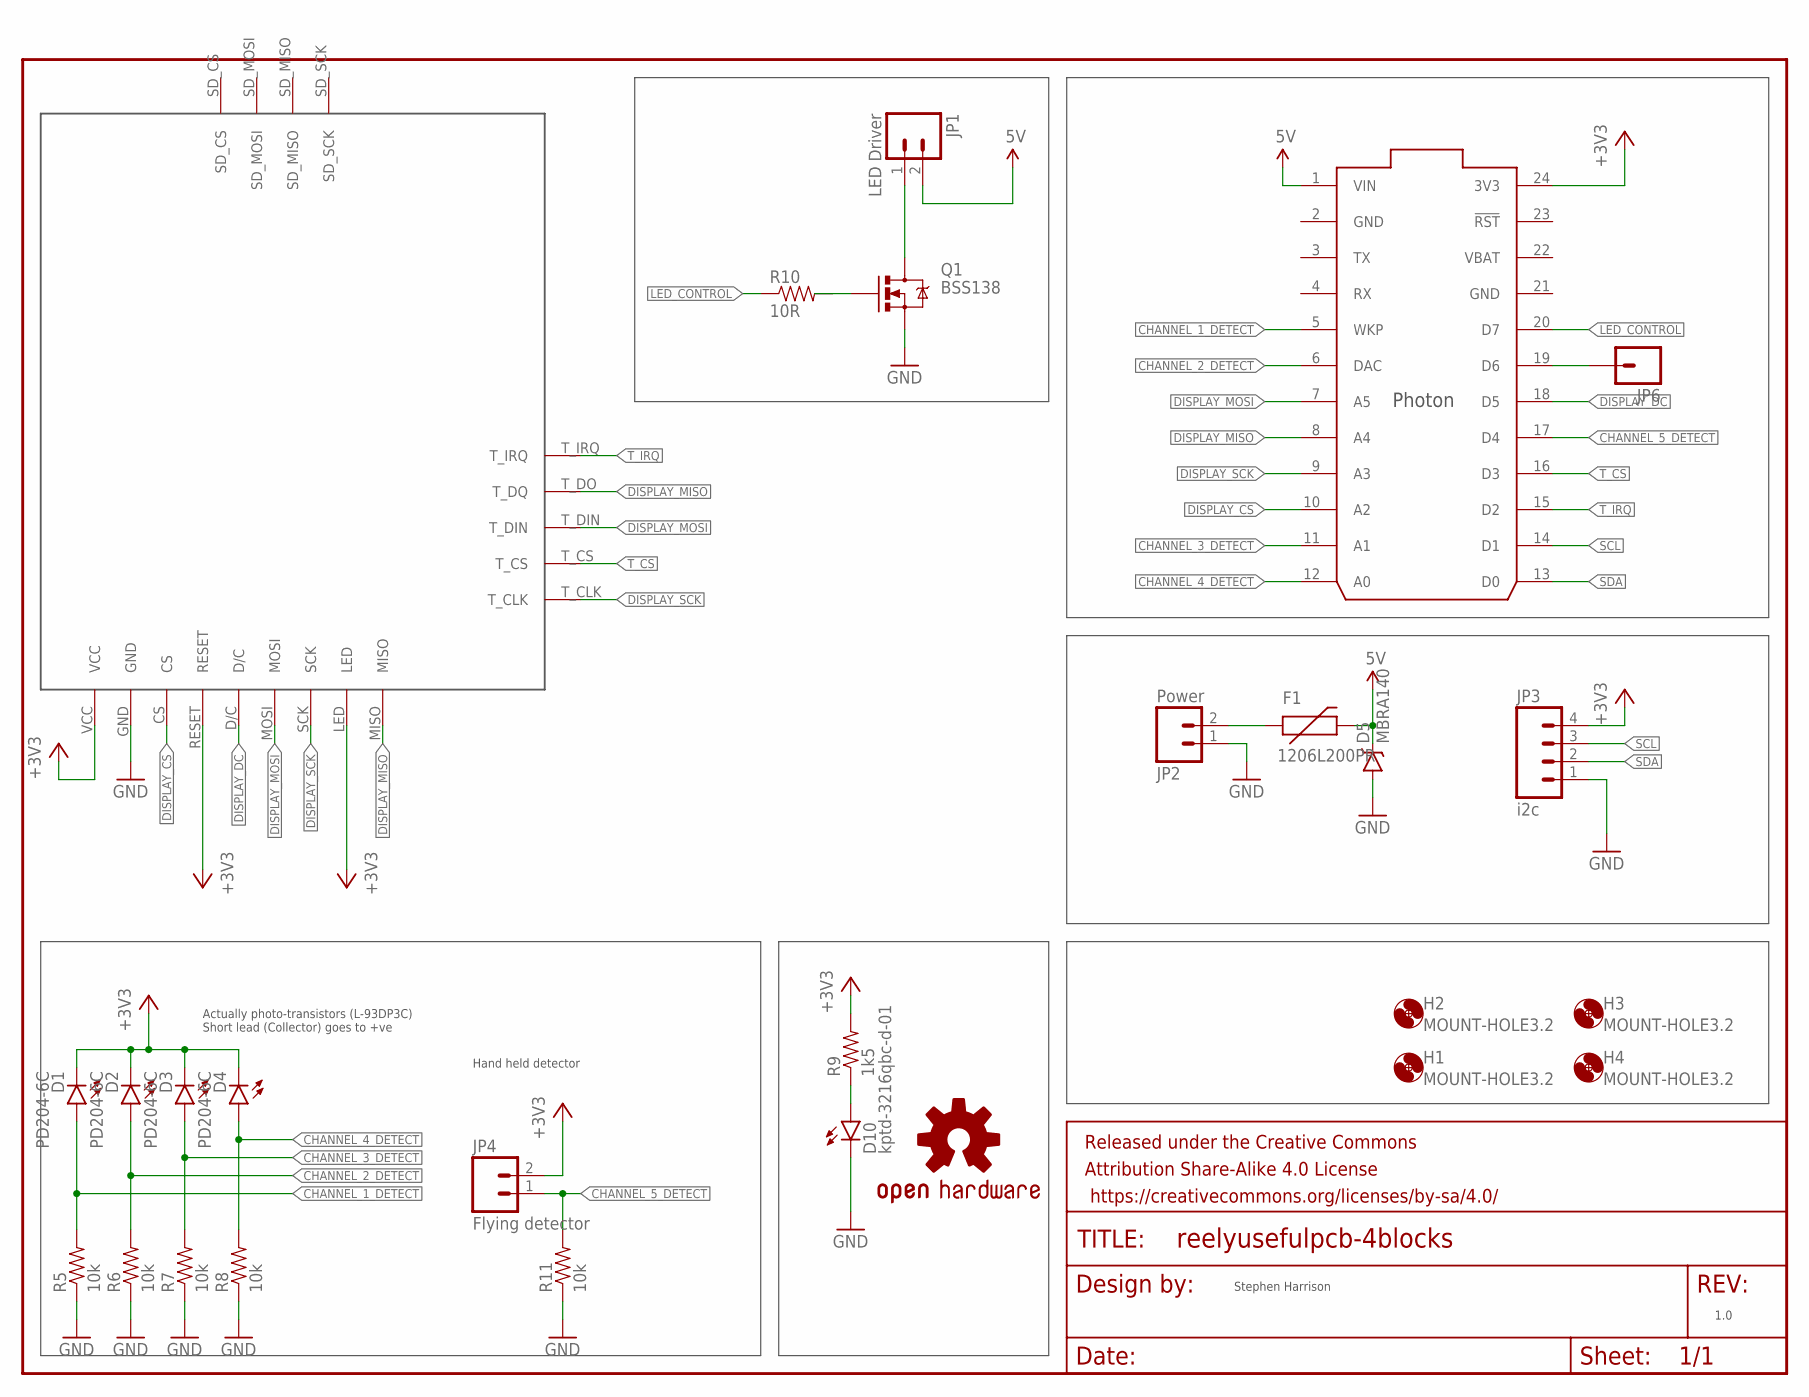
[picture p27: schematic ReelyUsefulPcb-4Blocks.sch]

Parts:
D1, D2, D3, D4: PD204-6C; LED3MM
D5: MBRA140; SMA-DIODE
D10: kptd-3216qbc-d-01; LED-1206-BOTTOM; FARNELL 2290349
F1: 1206L200PR; PTC-1206; FARNELL 2383297
FRAME1: FRAME-LETTER; CREATIVE_COMMONS
H1, H2, H3, H4: MOUNT-HOLE3.2; 3,2
JP1: LED Driver; JST-2-PTH
JP2: Power; JST-2-SMD
JP3: i2c; 1X04
JP4: Flying detector; JST-2-PTH
JP6: M01PTH; 1X01
LOGO1: OSHW-LOGOL; OSHW-LOGO-L
Q1: BSS138; SOT23-3; FARNELL 9845330
R5, R6, R7, R8, R11: 10k; 1206
R9: 1k5; 1206
R10: 10R; 1206
U2: TJCTM240
U3: PHOTON_SMD

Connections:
5V: D5.C, F1.2, JP1.2, U3.1 (VIN)
+3V3: D1.K (C), D2.K (C), D3.K (C), D4.K (C), JP3.4, JP4.2, R9.2, U2.LED, U2.RESET, U2.VCC, U3.24 (3V3)
CHANNEL_1_DETECT: D1.A, R5.2, U3.5 (WKP)
CHANNEL_2_DETECT: D2.A, R6.2, U3.6 (DAC)
CHANNEL_3_DETECT: D3.A, R7.2, U3.11 (A1)
CHANNEL_4_DETECT: D4.A, R8.2, U3.12 (A0)
CHANNEL_5_DETECT: JP4.1, R11.2, U3.17 (D4)
DISPLAY_CS: U2.CS, U3.10 (A2)
DISPLAY_DC: U2.D/C, U3.18 (D5)
DISPLAY_MISO: U2.MISO, U2.T_DO (T_DQ), U3.8 (A4)
DISPLAY_MOSI: U2.MOSI, U2.T_DIN, U3.7 (A5)
DISPLAY_SCK: U2.SCK, U2.T_CLK, U3.9 (A3)
GND: D5.A, D10.C, JP2.1 (2), JP3.1, Q1.2 (S), R5.1, R6.1, R7.1, R8.1, R11.1, U2.GND, U3.2 (GND), U3.21 (GND)
LED_CONTROL: R10.1, U3.20 (D7)
unnamed: D10.A, R9.1
unnamed: JP1.1, Q1.3 (D)
unnamed: JP6.1, U3.19 (D6)
unnamed: Q1.1 (G), R10.2
unnamed: F1.1, JP2.2 (1)
SCL: JP3.3, U3.14 (D1)
SDA: JP3.2, U3.13 (D0)
T_CS: U2.T_CS, U3.16 (D3)
T_IRQ: U2.T_IRQ, U3.15 (D2)
VBAT: U3.22 (VBAT)

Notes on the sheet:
Hand held detector
Actually photo-transistors (L-93DP3C) Short lead (Collector) goes to +ve
1.0
Stephen Harrison

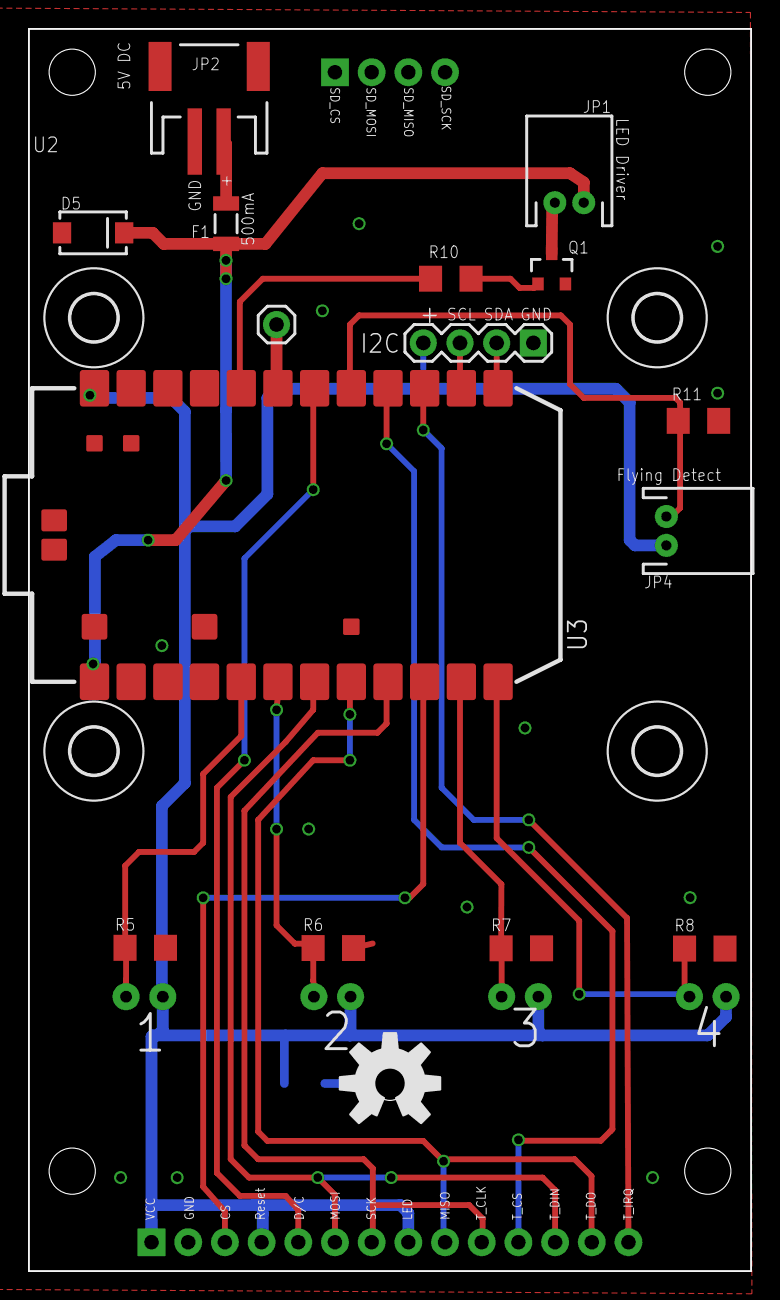
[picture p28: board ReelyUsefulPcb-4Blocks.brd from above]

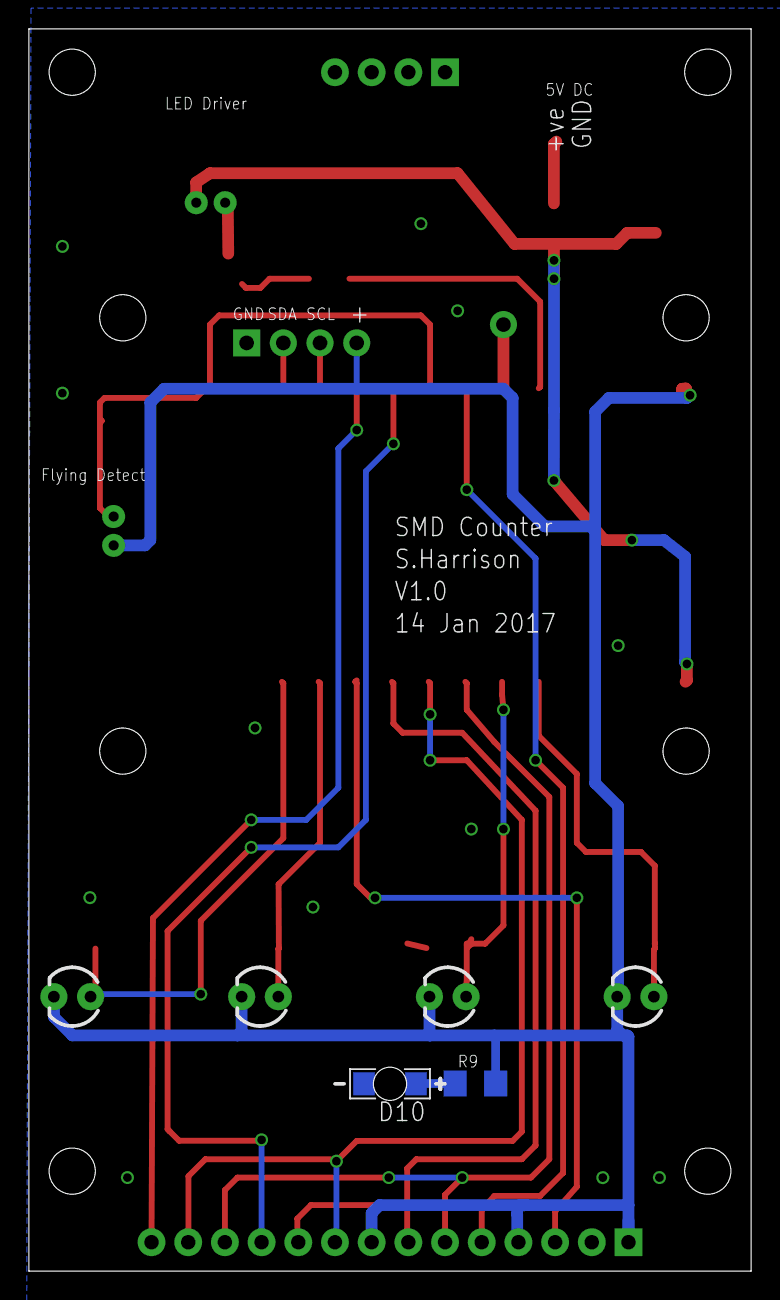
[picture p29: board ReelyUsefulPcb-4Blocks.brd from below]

Board: 2 copper layers, 50.0 x 86.0 mm, 28 parts (6 on the bottom side), 23 nets.

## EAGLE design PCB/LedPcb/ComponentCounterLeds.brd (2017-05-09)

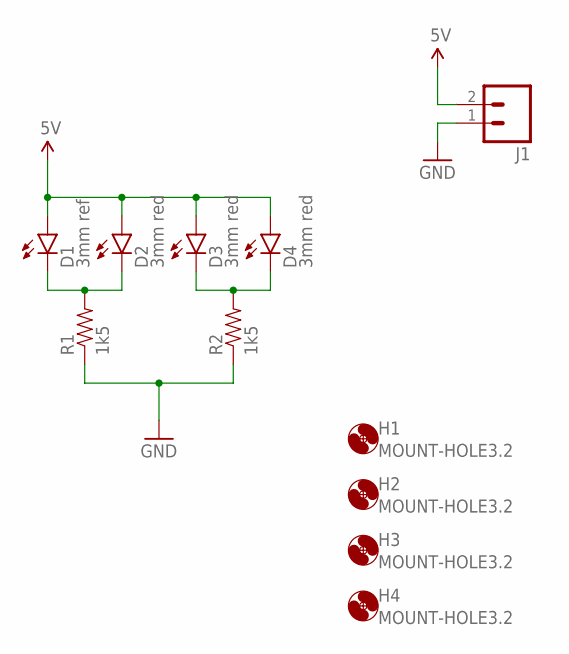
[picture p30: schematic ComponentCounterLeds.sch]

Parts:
D1: 3mm ref; LED3MM-NS
D2, D3, D4: 3mm red; LED3MM-NS
H1, H2, H3, H4: MOUNT-HOLE3.2; 3,2
J1: M02-JST-2MM-SMT; JST-2-SMD; FARNELL 9492615
R1, R2: 1k5; 1206

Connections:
5V: D1.A, D2.A, D3.A, D4.A, J1.2 (1)
GND: J1.1 (2), R1.1, R2.1
unnamed: D1.K (C), D2.K (C), R1.2
unnamed: D3.K (C), D4.K (C), R2.2

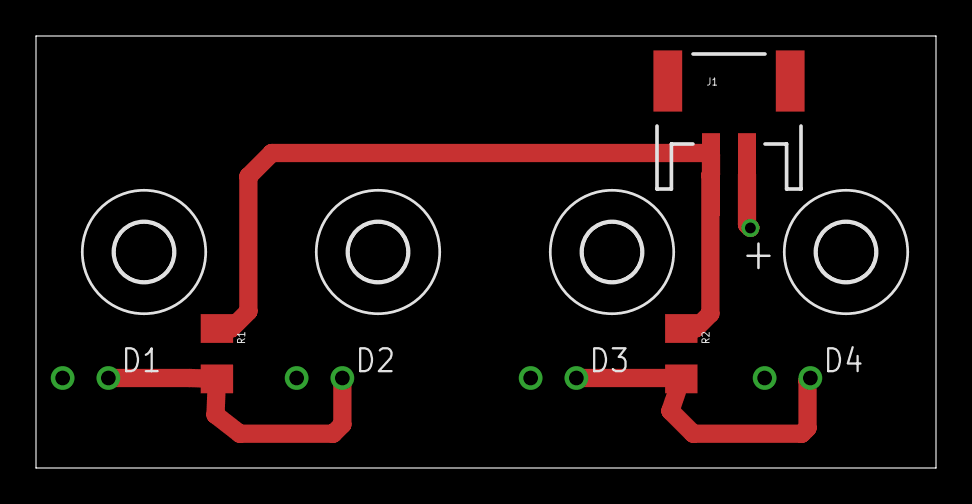
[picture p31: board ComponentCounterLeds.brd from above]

Board: 2 copper layers, 50.0 x 24.0 mm, 11 parts (0 on the bottom side), 4 nets.

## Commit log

2017-01-11 Work in progress initial version of SMD Reel holder.
    [ComponentUsageSensor.scad, MountingPlate.scad, ReelBlank.scad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]
2017-01-11 Removed material so that the riser arm can fit either side of the base.
    [ReelHolder2.scad]
2017-01-11 Made the LED hole a little smaller so the LED would fit snugly.
    [SMDReallyUsefulDispenser.scad]
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2017-01-12 Made the enterance cutout bigger to make it easier to feed the tape in.
    Changed exit cutout so it's actually a ramp so that the tape is pushed over the edge of the lid.
    [SMDReallyUsefulDispenser.scad]
2017-01-12 Increased the tollerance for the mating cylinder fits as 0.2 was tight and difficult to seperate.
    Renamed riser... to arm... as it better represents what it is.
    [ReelHolder2.scad]
2017-01-12 Added previous version of reel holders into Alternative folder.
    [ReelBlank.scad, ReelBlank.stl, ReelHolder.scad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]
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2017-01-12 Renamed SMDReallyUsefulDispenser to Dispenser and ReelHolder2 to ReelHolder.
    [Dispenser.scad, Dispenser.stl, ReelHolder-Arm.stl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]
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2017-01-12 Set to 25 reels (blocks).
    [MountingPlate.scad]
2017-01-14 Started to move common values out into its own Common.scad file.
    Changed tape height for counter block to slightly less than the enterance to the block on the dispenser.
    Shortened length to match change with new dispenser and so it's just longer than the display PCB.
    Improved screw holes.
    [Common.scad, ComponentUsageSensor.scad, ComponentUsageSensor.stl]
2017-01-15 Moved film removal block back a bit to fit the Counter PCB better and made it longer to allow for labeling to fit on it easily.
    Updated to use the Common.scad file for shared common values.
    Tidied up the code a bit.
    Changed screw hole #3 to allow for a hidden screw head underneath so that the arm top may be held in position by a screw and the dispencer removed.
    [Dispenser.scad, Dispenser.stl]
2017-01-15 Split ReelHolder to ReelHolder and ReelHolderArm files and updated stl's to match.
    Changed screw holes to support holding M3 nuts also so that the HeatFit inserts are not required for the reel holder top.
    Changed screw hole (well nut holder) to be deeper than the others as the screw has to go through the top component block as well and it's a long distance for a M3 screw.
    [ReelHolder-Arm.stl, ReelHolder-Top.stl, ReelHolder.scad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]
2017-01-15 Changed width to split out the actual desired spacing with and the printer tollerance allowance.
    [Common.scad]
2017-01-15 Reduced height as much as possible as it's going to be fairly tall with the display on.
    [ComponentUsageSensor.scad, ComponentUsageSensor.stl]
2017-01-15 Rebuild all the stls
    Added Build.bat to build all the stl's in one go.
    [ComponentUsageSensor.stl, Dispenser.stl, ReelHolder.stl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]
2017-01-24 Fixed tape wall width and the overall width.
    Removed dead code.
    [ReelHolder.scad, ReelHolder.stl]
2017-01-24 Rebuilt from scad file
    [ReelHolderArm.stl]
2017-01-24 Added PCB design for component counter add-on.
    *** Untested ***
    As sent to DirtyPCBs.
    [ReelyUsefulPcb-4Blocks.brd, ReelyUsefulPcb-4Blocks.sch]
2017-01-24 Fixed some sizing issues.
    [Dispenser.scad, Dispenser.stl]
2017-01-24 Added ability to use a pin to connect to the dispenser rather than screw as this works well when SLA printed.
    [ComponentUsageSensor-Pin.stl, ComponentUsageSensor.scad, ComponentUsageSensor.stl]
2017-01-24 Updated tollerance for printing nad added tape hole offset.
    [Common.scad]
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2017-01-28 Reduced printer tollerance gap slightly.
    Increased gap in cylinder mating for the reel holder arm.
    rebuilt stl's.
    [Common.scad, ComponentUsageSensor-Pin.stl, ComponentUsageSensor.stl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]
2017-01-30 Added numberOfBlocksWide to specify how many units of block width (13mm) the arm/reel holder/dispencer/component counter should be to allow for wide tape (LEDs etc).
    [Common.scad]
2017-01-30 Rounded the edge of the tape enterance and added box that should sit inside the lid lip to give a nicer finish.
    Added numberOfBlocksWide to specify how many units of block width (13mm)
    Modified m3/pin from component sensor holes so they stay at a fixed Z and do not move with tape height.
    [Dispenser.scad]
2017-01-30 Set to use common values rather than having it's own block width.
    Modified to support multi-block width reel holder and kept contact area to small size.
    [ReelHolderArm.scad]
2017-01-30 Added support for multiple block width.
    Added curve to tape enterance to stop LED tape snagging.
    [ReelHolder.scad]
2017-01-30 Added support for multi-block and tapeWidth.
    It might be wide tape (e.g. 12mm LED) which needs 2 blocks but the tape needs to be kept with the correct path.
    [ComponentUsageSensor.scad]
2017-01-30 Added repetition for LED hole to multi-block width as they can be used for drill tempate and possibly a PCB underneath to hold the LEDs in the future.
    [ReelHolder.scad]
2017-01-30 Reduced size for tape feed enterance and made the marker optional with the curve to the enterance always.
    [Dispenser.scad]
2017-01-30 Restored to 1 block wide by default.
    [Common.scad]
2017-01-30 Added LED holes for multiblock widths so that if a PCB is used to insert the LEDs then holes still exist for the led to align into.
    [Dispenser.scad]
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2017-02-14 Updated build to include a LED tape dispencer with larger gap.
    [ComponentUsageSensor-Pin-4Wide-MultiTape.stl, ComponentUsageSensor-Pin-LED.stl, ComponentUsageSensor-Pin.stl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]
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2017-05-09 Added the LED PCB.
    [ComponentCounterLeds.brd, ComponentCounterLeds.sch]
2017-05-22 Refacotred the arm so that the coordinates make more sense.
    Dropped width to 1mm as 2mm is a bit to big with the reels fitted.
    [ReelHolderArm.scad]
2017-05-22 Improved component sensor to allow a nut to be inserted horizontally for fixing the PCB otherwise the nut needs to be in before this is screwed to the case which is difficult.
    Opneed up more space on the board to allow for pins.
    [ComponentUsageSensor.scad]
2017-08-17 Rebuilt stls. made arm thinner as it is a little too wide and causes the reels to be larger than their allowed area.
    Improvements in dispenser for multi block width units.
    [ComponentUsageSensor-Pin-4Wide-MultiTape.stl, ComponentUsageSensor-Pin-LED.stl, ComponentUsageSensor-Pin.stl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]
2017-08-17 Monior improvements to pcb/schematic names and values.
    [ReelyUsefulPcb-4Blocks.brd, ReelyUsefulPcb-4Blocks.sch]
2017-08-17 Added case for the display unit.
    [DisplayCase.scad, DisplayCase.stl]
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2017-08-17 Added ComponentCatcher to build.bat file.
    Created stl for component catcher.
    [ComponentCatcher.stl]
2018-10-01 Changed each spool block width to 15mm to give more space for the spools.
    [Common.scad, ComponentCatcher.scad, ComponentCatcher.stl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]
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

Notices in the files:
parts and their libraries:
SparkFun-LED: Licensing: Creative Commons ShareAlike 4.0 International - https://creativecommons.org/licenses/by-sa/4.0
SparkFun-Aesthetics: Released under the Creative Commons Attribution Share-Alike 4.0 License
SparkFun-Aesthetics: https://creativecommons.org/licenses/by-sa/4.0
